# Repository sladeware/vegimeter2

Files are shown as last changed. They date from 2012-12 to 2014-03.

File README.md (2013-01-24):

<!--- -*- coding: utf-8; mode: markdown; -*- --->

Vegimeter

Copyright (c) 2011-2013 Sladeware LLC

http://www.bionicbunny.org/

What is Vegimeter?
------------------

The purpose of the Vegimeter application is to use the minimal amount of energy
to heat a container of potting soil to within a specific temperature range, with
the assumption that the ambient temperature is below the desired range so that
heating the soil is required. This is to provide nearly ideal soil temperature
to plants' roots so as to optimize their nutrient transport.

Please visit <https://sites.google.com/site/vegimeter2/> and
<http://www.bionicbunny.org> to learn more about Vegimeter device.

Documents
---------

* [Design document](https://docs.google.com/document/d/15U6fNcfc0FeTir46BejYtf14oOK8b4B83Xh8CfdANuI/edit)
* [Architecture document](https://docs.google.com/drawings/d/1-p6k4T24JzqQ8bxHXnyh6eOs4cmtS7jffa-5HD3LI7g/edit)

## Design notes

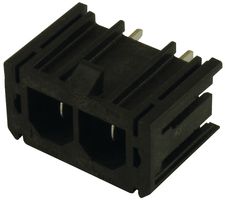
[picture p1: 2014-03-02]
images/molex-43160-0102.jpg

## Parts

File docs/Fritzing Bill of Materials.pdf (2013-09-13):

9/13/13 | Fritzing Bill of Materials
file:///home/slade/Documents/vegimeter2/vegimeter2_bom.html | 1/4

# Bill of Materials: vegimeter2.fzz

/home/slade/git/vegimeter2/device/vegimeter2.fzz
Friday, September 13 2013, 01:23:09

# Assembly List

Label | Part Type | Properties
0.1 uF | Capacitor | package cappthsmall2; variant pth2
5 MHz XTAL | CRYSTAL | package hc49us; variant hc49us
Air Temp | TEMPERATURE- SENSOR | package to-92; part # DS18B20
C2 (10 nF) | Capacitor | package cappthsmall2; variant pth2
C3 (4.7uF) | Capacitor | package cappthsmall2; variant pth2
EEPROM | 24LC256 | package THT; interface I2C; variant 24LC256
FT232RL | USB UART | package ssop28db; chip FT232RL; variant ssop
Heater | Power plug
Heater Relay | RELAY | package relayjzc; variant pth4
LR 3.3V | Voltage Regulator 3.3V | package TO220 [THT]; voltage 3.3V; part # LM7833
LR 5.0V | SPX29302 | package q5-dd_spx29300; features LDO; current 3A; part # SPX29300T-L-5-0
Mini USB | USB Connectors | package usbbpth; target USB-B; variant pth
NPN | NPN-Transistor | package TO92 [THT]; type NPN (EBC)
Primary | Power plug
Propeller1 | Parallax Propeller D40 | package DIP [THT]; type Parallax Propeller
Pump | Power plug

file:///home/slade/Documents/vegimeter2/vegimeter2_bom.html | 2/4
Pump Relay | RELAY | package relayjzc; variant pth4
R1 | 10k Ω Resistor | package THT; tolerance ±5%; bands 4; resistance 10kΩ; pin spacing 400 mil
R2 | 10k Ω Resistor | package THT; tolerance ±5%; bands 4; resistance 10kΩ; pin spacing 400 mil
R3 | 10k Ω Resistor | package THT; tolerance ±5%; bands 4; resistance 10kΩ; pin spacing 400 mil
R4 | 4.7k Ω Resistor | package THT; tolerance ±5%; bands 4; resistance 4.7kΩ; pin spacing 400 mil
R5 | 4.7k Ω Resistor | package THT; tolerance ±5%; bands 4; resistance 4.7kΩ; pin spacing 400 mil
R6 | 4.7k Ω Resistor | package THT; tolerance ±5%; bands 4; resistance 4.7kΩ; pin spacing 400 mil
R7 | 4.7k Ω Resistor | package THT; tolerance ±5%; bands 4; resistance 4.7kΩ; pin spacing 400 mil
R8 | 4.7k Ω Resistor | package THT; tolerance ±5%; bands 4; resistance 4.7kΩ; pin spacing 400 mil
R9 | 4.7k Ω Resistor | package THT; tolerance ±5%; bands 4; resistance 4.7kΩ; pin spacing 400 mil
R11 | 1k Ω Resistor | package THT; tolerance ±5%; bands 4; resistance 1kΩ; pin spacing 400 mil
R12 | 220 Ω Resistor | package THT; tolerance ±5%; bands 4; resistance 220Ω; pin spacing 400 mil
R13 | 220 Ω Resistor | package THT; tolerance ±5%; bands 4; resistance 220Ω; pin spacing 400 mil
R14 | 100 Ω Resistor | package THT; tolerance ±5%; bands 4; resistance 100Ω; pin spacing 400 mil
R15 | 10k Ω Resistor | package THT; tolerance ±5%; bands 4; resistance 10kΩ; pin spacing 400 mil
R16 | 4.7k Ω Resistor | package THT; tolerance ±5%; bands 4; resistance 4.7kΩ; pin spacing 400 mil

### Reset

### SWITCH-MOMENTARY-2

| | package tactile_switch_tall

### Soil A Temp

| Header 3 | package screwterminal-3.5mm-3_lock.007s; variant screw_lock

### Soil B Temp

| Header 3 | package screwterminal-3.5mm-3_lock.007s; variant screw_lock

file:///home/slade/Documents/vegimeter2/vegimeter2_bom.html | 3/4

### Soil C Temp

| Header 3 | package screwterminal-3.5mm-3_lock.007s; variant screw_lock
Soil D Temp | Header 3 | package screwterminal-3.5mm-3_lock.007s; variant screw_lock
ULN2803A | ULN2803A | package THT; variant ULN2803A
USB RX | LEDs | package led10mm; variant 10mm
USB TX | LEDs | package led10mm; variant 10mm
Water A Temp | Header 3 | package screwterminal-3.5mm-3_lock.007s; variant screw_lock
Water B Temp | Header 3 | package screwterminal-3.5mm-3_lock.007s; variant screw_lock
XBEE | XBee | model XBee ZNet 2.5; pins 20
XBEE In | LEDs | package led10mm; variant 10mm
XBEE Out | LEDs | package led10mm; variant 10mm

# Shopping List

Amount | Part Type | Properties
3 | Capacitor | package cappthsmall2; variant pth2
1 | CRYSTAL | package hc49us; variant hc49us
1 | TEMPERATURE- SENSOR | package to-92; part # DS18B20
1 | 24LC256 | package THT; interface I2C; variant 24LC256
1 | USB UART | package ssop28db; chip FT232RL; variant ssop
3 | Power plug
2 | RELAY | package relayjzc; variant pth4
1 | Voltage Regulator 3.3V | package TO220 [THT]; voltage 3.3V; part # LM7833
1 | SPX29302 | package q5-dd_spx29300; features LDO; current 3A; part # SPX29300T-L-5-0

file:///home/slade/Documents/vegimeter2/vegimeter2_bom.html | 4/4
1 | USB Connectors | package usbbpth; target USB-B; variant pth
1 | NPN-Transistor | package TO92 [THT]; type NPN (EBC)
1 | Parallax Propeller D40 | package DIP [THT]; type Parallax Propeller
4 | 10k Ω Resistor | package THT; tolerance ±5%; bands 4; resistance 10kΩ; pin spacing 400 mil
7 | 4.7k Ω Resistor | package THT; tolerance ±5%; bands 4; resistance 4.7kΩ; pin spacing 400 mil
1 | 1k Ω Resistor | package THT; tolerance ±5%; bands 4; resistance 1kΩ; pin spacing 400 mil
2 | 220 Ω Resistor | package THT; tolerance ±5%; bands 4; resistance 220Ω; pin spacing 400 mil
1 | 100 Ω Resistor | package THT; tolerance ±5%; bands 4; resistance 100Ω; pin spacing 400 mil

1

### SWITCH-MOMENTARY-2

| | package tactile_switch_tall
6 | Header 3 | package screwterminal-3.5mm-3_lock.007s; variant screw_lock
1 | ULN2803A | package THT; variant ULN2803A
4 | LEDs | package led10mm; variant 10mm
1 | XBee | model XBee ZNet 2.5; pins 20

Exported with Fritzing 0.8.3- http://fritzing.org

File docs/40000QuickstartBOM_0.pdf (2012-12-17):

Part Number: 40000 | Product Owner: David Carrier
Latest Revision: A3 | Last Updated: 5/6/2011
Reference Manufacturer Stock Code Quantity Designator Description or Supplier Orderable Part Number | Notes
124-40000 | 1 | Box Sleeve, QuickStart
150-11031 | 5 R1-R5 | RES,10K,5%,0603
150-11045 | 1 R6 | RES,220,5%,0603
172-01010 | 1 R7 | RES,100,5%,0603
172-15007 | 2 R12-R13 | RES,0 OHM,0603, 1/10W | Digi-Key | RMCF0603ZT0R00TR-ND
179-10610 | 2 R8-R9 | RES-NTWK,100K,0612 | Digi-Key | YC164J-100KTR-ND
179-10611 | 2 R10-R11 | RES-NTWK,240,0612 | Digi-Key | YC164J-240TR-ND
210-10001 | 2 C12-C13 | CAP-CER,10uF,16V,Y5V,1210 | Digi-Key | 445-1597-6-ND
213-01040 | 10 C1-C10 | CAP-CER,0.1uF,20%,25V,Y5V,0603
213-04761 | 1 C11 | CAP-CER,4.7uF,20%,10V,X5R,060
251-15000 | 1 X1 | CRYSTAL 5.000 MHZ 18PF SMD
300-40000 | 1 | Raw, PCB, QuickStart
350-10001 | 1 D10 | LED 0603, Super Red Clear-LF
350-10003 | 1 D11 | LED 0603, Green Clear-LF
350-10004 | 9 D1-D9 | LED 0603, Blue Clear LF
400-10003 | 1 S1 | Tact Switch SMD-LF
452-10006 | 1J2 | CON,USB Mini-B,SMD
452-11001 | 1J1 | COM-HDR,2X20,SMD,0.1" | Digi-Key | 68046-620LF-ND
500-10011 | 1 Q2 | MOSFET P-CH 20V 3.7A SOT-23
500-10019 | 1 Q1 | TRN-NPN 2N3904,SOT-23
501-10018 | 1 D12 | DIODE,SCHOTTKY,20V,1A,DO-214AC | Digi-Key | 641-1014-6-ND
601-10335 | 1 VR1 | IC-REG,3.3V,1A,SOT223
602-10017 | 1 U2 | IC Microchip 24LC256-I/ST - LF
603-10008 | 1 U4 | 74LVC126A | Digi-Key | 568-2288-6-ND
603-10009 | 1 U5 | 74HC541 | Digi-Key | 296-8335-6-ND
604-00043 | 1 U3 | FTDI 232 RL
P8X32A-Q44 | 1 U1 | P8X32A-Q44 (QFP)
X10-00300 | 1 | Bag ESD Heat Pink 6x4

# Bill of Materials — P8X32A QuickStart

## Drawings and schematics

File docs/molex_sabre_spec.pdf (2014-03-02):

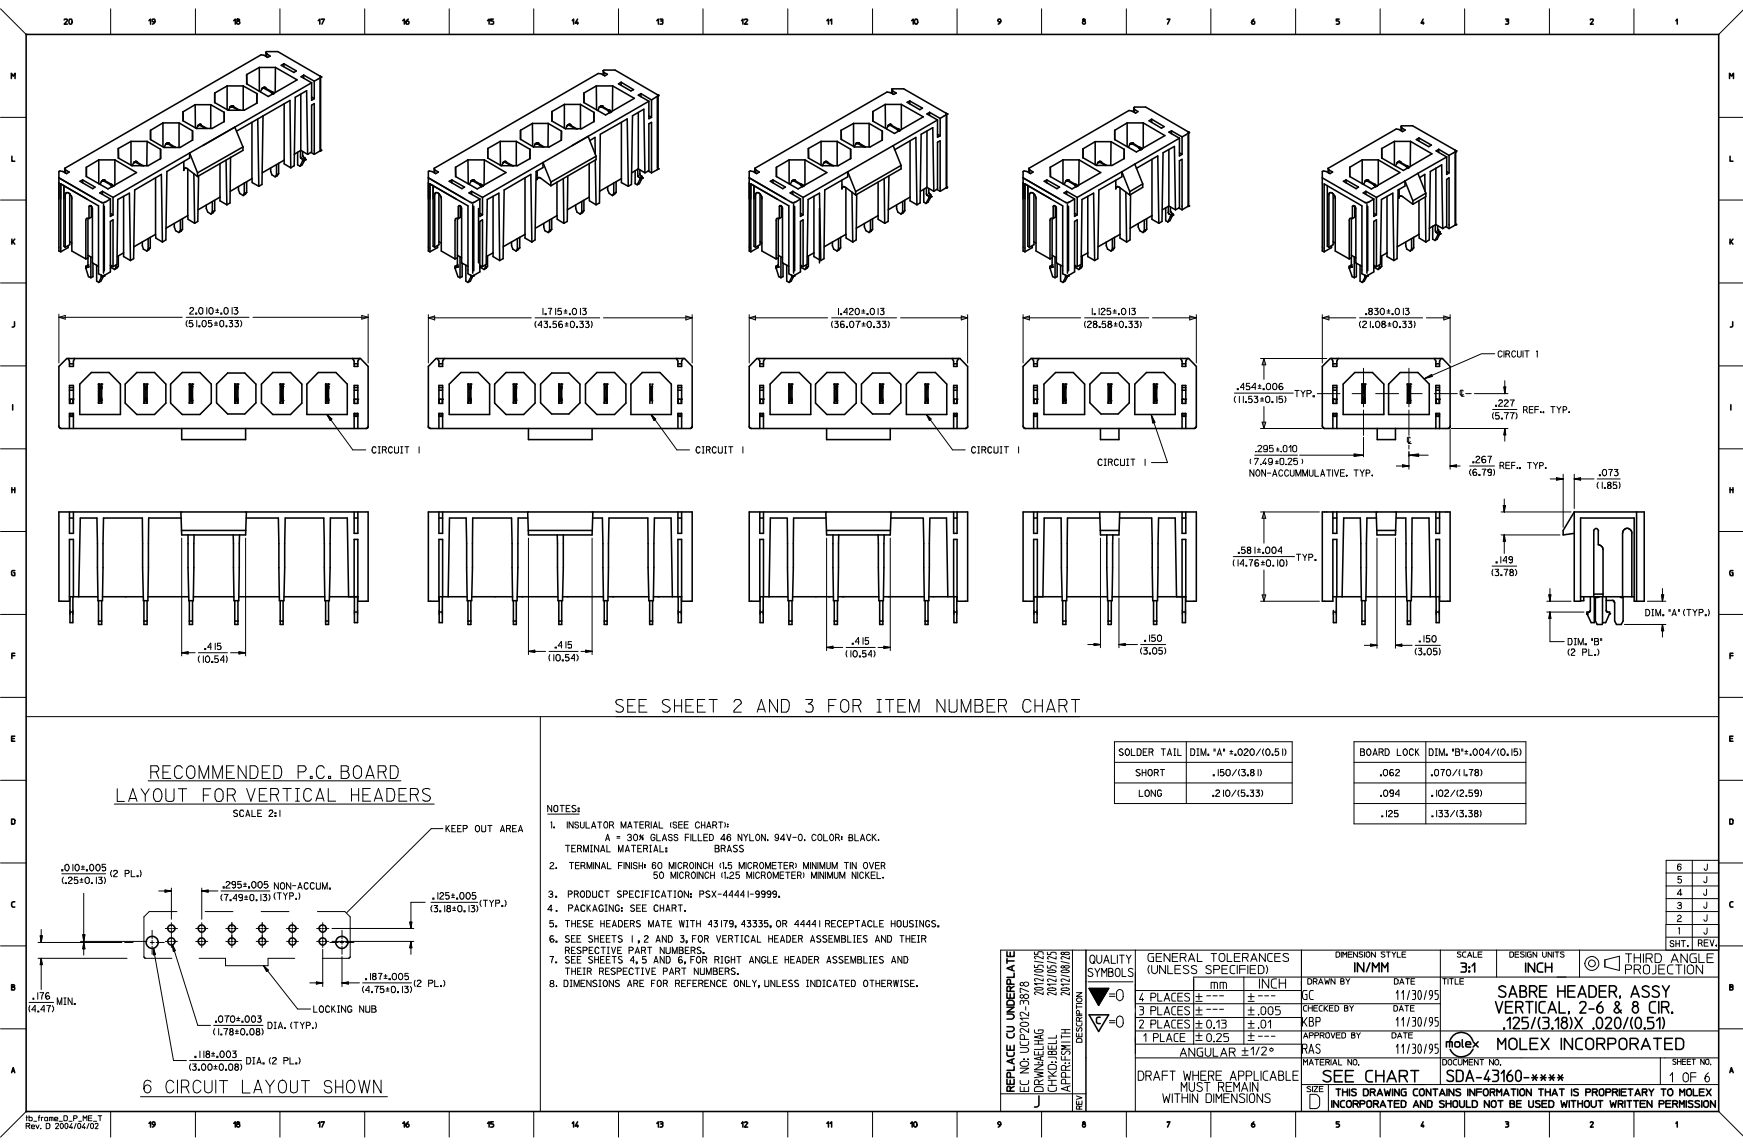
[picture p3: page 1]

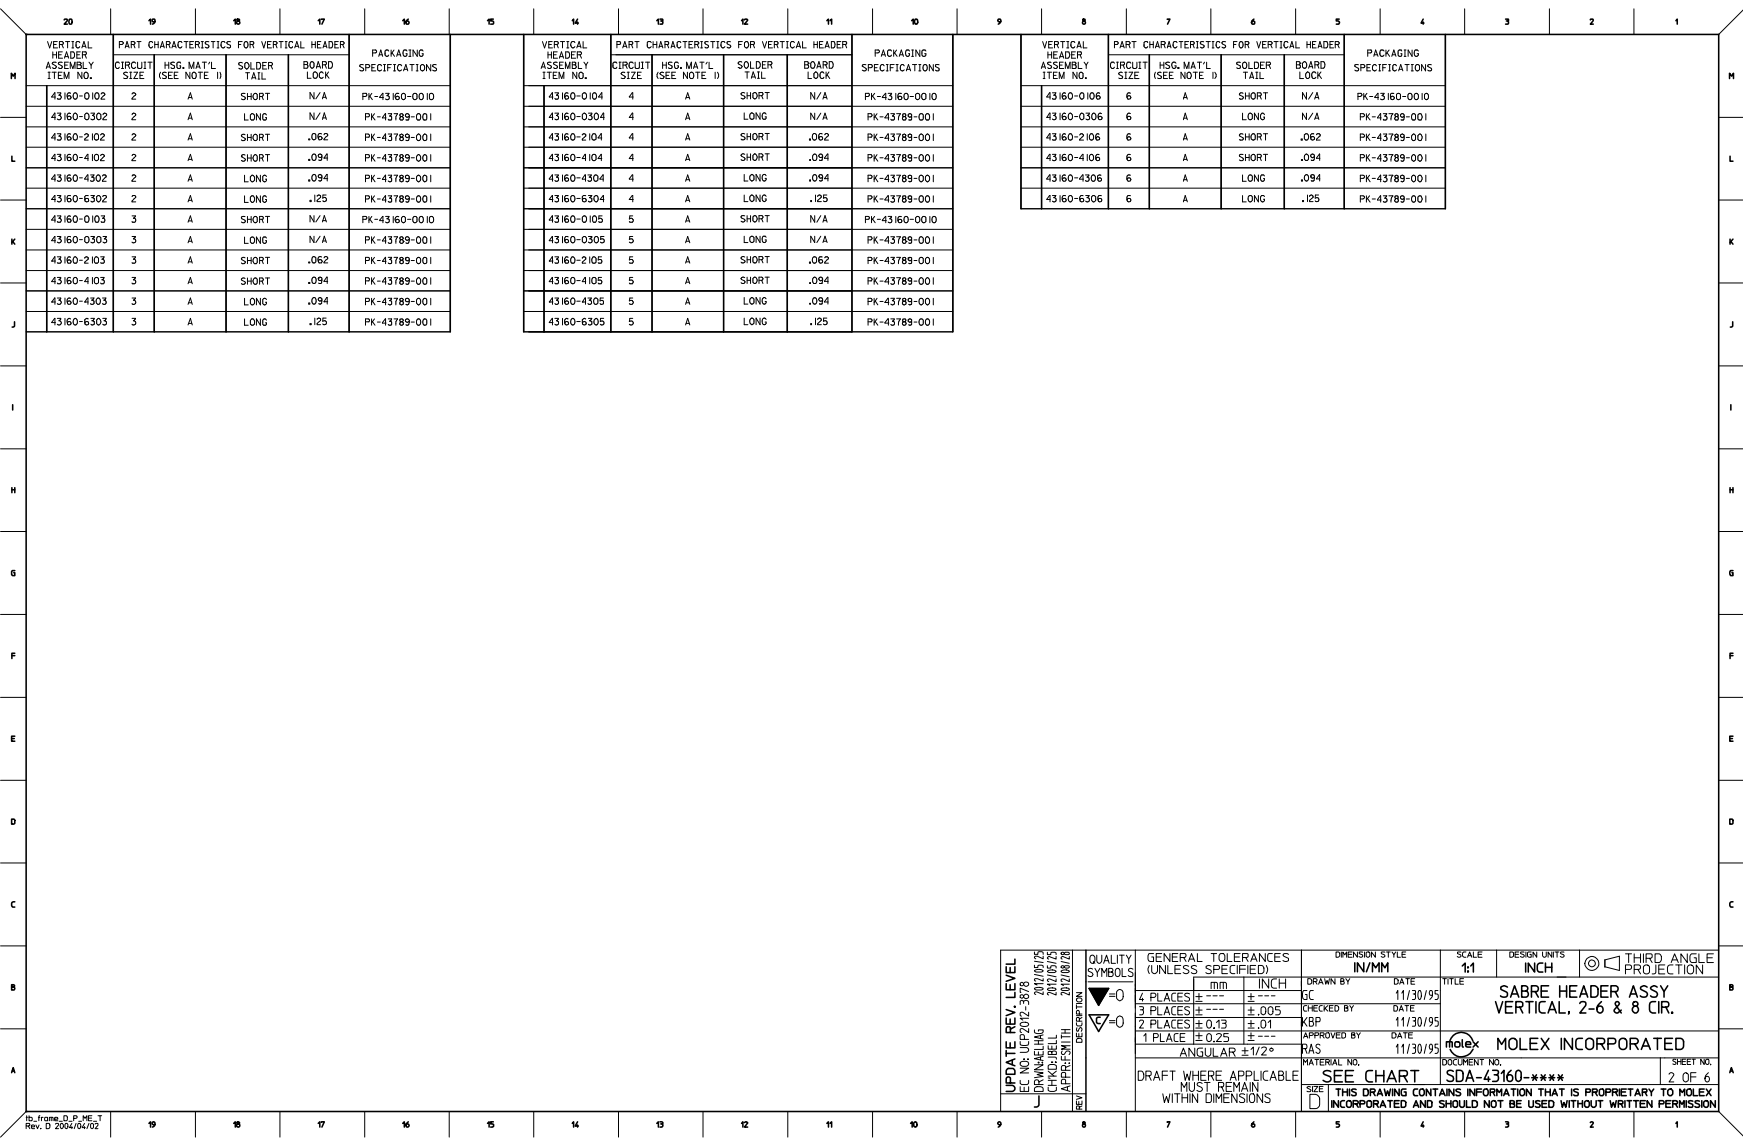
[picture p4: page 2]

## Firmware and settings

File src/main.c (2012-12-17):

/* Copyright 2011 Sladeware LLC
 *
 * Licensed under the Apache License, Version 2.0 (the "License");
 * you may not use this file except in compliance with the License.
 * You may obtain a copy of the License at
 *
 *     http://www.apache.org/licenses/LICENSE-2.0
 *
 * Unless required by applicable law or agreed to in writing, software
 * distributed under the License is distributed on an "AS IS" BASIS,
 * WITHOUT WARRANTIES OR CONDITIONS OF ANY KIND, either express or implied.
 * See the License for the specific language governing permissions and
 * limitations under the License.
 */

/* This will eventually be replaced by real BBOS schedulers and running on multiple cogs */

#include <bb/os.h>
#include <bb/os/kernel/delay.h>
#include <vegimeter.h>

int
main()
{
  unsigned delay = 1000; /* ms */
  unsigned vegimeter_buttons = 0;
  int water_temperature = 0;
  int soil_temperature_a = 0;
  int soil_temperature_b = 0;
  int soil_temperature_c = 0;
  int soil_temperature_d = 0;
  unsigned heater_on = 0;
  unsigned pump_on = 0;

  printf("Starting Vegimeter!\n");

  do {
    controller_runner(water_temperature, soil_temperature_a, soil_temperature_b,
                      soil_temperature_c, soil_temperature_d,
                      soil_temperature_d, &heater_on, &pump_on);

    /* Button presses are hard detect until we're in a non-blocking context */
    vegimeter_buttons = button_driver_runner();

    heater_driver_runner(heater_on);
    pump_driver_runner(pump_on);

    water_temperature = temp_sensor_driver_water_runner();
    soil_temperature_a = temp_sensor_driver_soil_a_runner();
    soil_temperature_b = temp_sensor_driver_soil_b_runner();
    soil_temperature_c = temp_sensor_driver_soil_c_runner();
    soil_temperature_d = temp_sensor_driver_soil_d_runner();

    ui_runner(water_temperature, soil_temperature_a, soil_temperature_b,
              soil_temperature_c, soil_temperature_d,
              soil_temperature_d, vegimeter_buttons);

    printf("Sleeping for %d ms\n", delay);
    bbos_delay_msec(delay);
  } while(1);

  return 0;
}

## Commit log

2012-12-17 Move vegimeter project source from bbos projects.
    [device.fz, device.fzz]
2013-01-24 Put fz device design and parts under device.
    [device.fz, device.fzz]
2013-09-13 Created Vegimeter 2 Revision 0 board. This is the version sent to Fritzing fabrication.
    [device.fz, device.fzz, vegimeter2.fzz]
2013-11-25 Rev 1 Vegimeter 2 Fritzing PCB as submitted to Fab. V0 of the Vegimeter 2 software.
    [vegimeter2.fzz]
2013-12-09 Added 1K for long temp sensor probes.
    [vegimeter2.fzz]
2013-12-16 Revision 2 PCB. Fixes bug in powering USB.
    [vegimeter2.fzz]
2014-02-09 Ultimately I connected a QuickStart board to the Vegimeter 2 Rev 2 board to get this working and had to remap the pins. This is the remapping. Good news, Vegimeter 2 is alive
2014-03-02 Draft of Vegimeter 2 Rev 3 Board with docs.
    This version supports a Parallax QuickStart board directly attached to
    the greatly simplified main Vegimeter board. Additionally, we have a
    much greater heater power capacity thanks to 3x relays and independent
    and parallel voltage rails. After studying the prior revision for a
    week, I moved the parts around to optimize heat flow and reduce the
    trace length of higher power traces. I made all higher power traces
    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
    [Untitled Sketch.fzz, vegimeter2.fzz]
2014-03-02 Cleanup of vegimeter 2 rev 3
    [vegimeter2.fzz]
2014-03-02 Final revision of Vegimeter 2 Rev 3. Submitted to Fritzing.
    This is pre-printout verification. There may be additional changes.
    [vegimeter2.fzz]
2014-04-20 Lengthened the time until system error occurs when heating water. Added better LED diagnostics. A few other tweaks based on trying out the code on a real device grwoing real veggies.
